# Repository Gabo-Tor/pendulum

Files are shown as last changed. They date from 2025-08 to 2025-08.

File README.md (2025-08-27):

# Actuated Pendulum with Propeller

A robot designed for reinforcement learning and control experiments with real hardware.

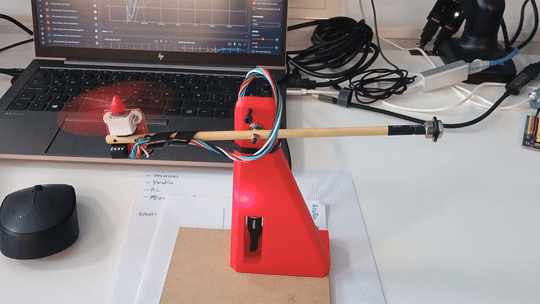
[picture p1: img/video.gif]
Video


# Repository Map

* **train.py**: training script for the robot.
* **hardware/**: 3D-printable models for the structure.
* **firmware/**: Arduino code for the ESP32 microcontroller.
* **test\_robot.py**: testing script for the robot.
* **env.py**: Gymnasium environment definition.
* **wrappers.py**: environment wrappers.

# Getting Started

## Hardware

### Bill of Materials

| Item | Description |
| --- | --- |
| ESP32 (Dev Kit C) | Microcontroller. Several board sizes are available on the market. We use the 25.70 × 53.40 mm version, but you may need to adapt the design for your board. |
| MG996R + propeller kit | Servo with motor, propeller, and controller. |
| AS5600 | Rotary encoder. |
| [3D-printed structure](hardware/body.stl) | Printed support structure. |
| 2 × M3 locking nuts | Fasteners. |
| 2 × M3×25 screws | Fasteners. |
| 623z | Bearing. |
| Flexible 4-wire cable | Electrical connection. |
| Wooden or cardboard base | Base, approximately 120 × 100 mm. |
| Counterweight | It has to still fall when left alone, but helps the actuator lift the pendulum. A M6 bolt, washer and nut was used in our case. |

### Assembly

* Connect the VCC pins of the MG996R and AS5600 to the 3.3 V pin on the ESP32.
* Connect all GND pins together, and w
* Connect the signal pins to the appropriate GPIOs on the ESP32 (as specified in *firmware.ino*).
* Glue the encoder magnet to the end of the screw that acts as the shaft.
* Some boards may require a small amount of glue to remain securely in place.

Assembled Robot

## Firmware

Upload the firmware to the ESP32 using the Arduino IDE.

## Usage

1. Install the required Python packages:

   ```bash
   pip install -r requirements.txt
   ```
2. Verify that everything is working by running:

   ```bash
   python test_robot.py
   ```

   The robot should move in a somewhat random manner.
3. Start training with:

   ```bash
   python train.py
   ```

# Reinforcement Learning

## History Wrapper

A history wrapper is used to maintain the last observations and actions taken by the agent.
This provides the agent with short-term memory and context, effectively restoring the Markov property of the environment. This is necessary because certain state variables (such as \$\dot{\theta}\$ or the propeller speed) are not directly observable from a single timestep.

## State-Space Representation

If we assume the propeller speed \$\omega\_p\$ is directly controllable (not entirely realistic), the system can be represented as:

$$
\mathbf{x} = \begin{bmatrix}\theta\\ \dot\theta\end{bmatrix},\qquad \omega_p = f(u).
$$

Dynamics:

$$
\dot{\mathbf{x}} =
\begin{bmatrix}
\dot\theta \\
\displaystyle \frac{1}{J}\Big( lc_T\omega_p^2 - m g l \sin\theta - b\dot\theta \Big)
\end{bmatrix}
$$

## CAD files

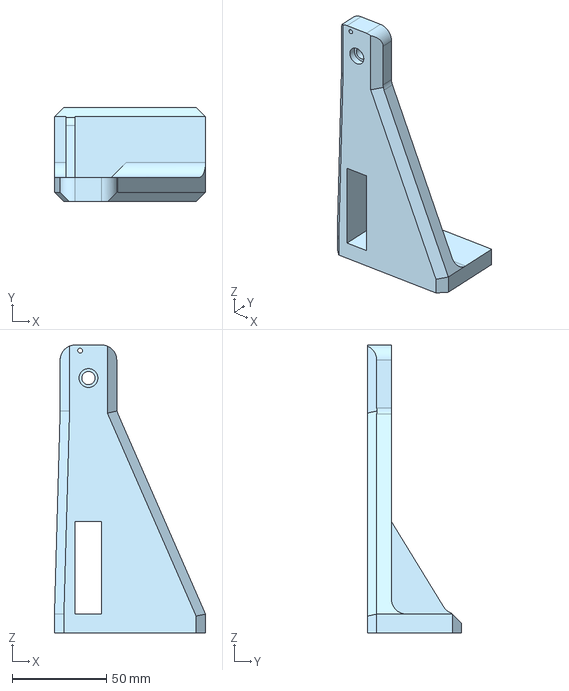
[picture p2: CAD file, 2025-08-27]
hardware/body.step
80.0 x 50.0 x 152.5 mm

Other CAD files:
hardware/body.stl

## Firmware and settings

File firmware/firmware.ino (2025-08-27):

#include <Wire.h>
#include "AS5600.h"

// === Pin Definitions ===
#define A_IN1 19   // L9110H Motor Driver INA
#define A_IN2 18   // L9110H Motor Driver INB
#define SDA 21  // I2C SDA pin for AS5600
#define SCL 22  // I2C SCL pin for AS5600

// === Constants ===
#define ZERO_ANGLE_OFFSET 869           // Calibration offset (raw units from AS5600) 0 is vertical
#define MAX_MOTOR_SPEED   255           // Max PWM value
#define MIN_MOTOR_SPEED   0

// === Globals ===
AS5600 as5600;
int currentMotorCmd = 0;  // Last received command (range -255 to 255)

// === Helper Functions ===

// Set motor output based on command value
void setMotor(int cmd) {
  cmd = constrain(cmd, -MAX_MOTOR_SPEED, MAX_MOTOR_SPEED);

  if (cmd > 0) {
    analogWrite(A_IN1, cmd);
    analogWrite(A_IN2, 0);
  } else if (cmd < 0) {
    analogWrite(A_IN1, 0);
    analogWrite(A_IN2, -cmd);  // use magnitude
  } else {
    analogWrite(A_IN1, 0);
    analogWrite(A_IN2, 0);
  }
}

// Read pendulum angle in degrees
float readAngle() {
  long rawAngle = as5600.readAngle();
  float angleDeg = (rawAngle - ZERO_ANGLE_OFFSET) * AS5600_RAW_TO_DEGREES;
  return angleDeg;
}

// Handle incoming serial command
void handleSerial() {
  if (Serial.available() > 0) {
    String input = Serial.readStringUntil('\n'); // Expect one line per action
    input.trim();

    if (input.length() > 0) {
      int cmd = input.toInt();   // Action = integer motor command
      currentMotorCmd = cmd;
      setMotor(currentMotorCmd);

      // Immediately respond with observation
      float angleDeg = readAngle();
      Serial.println(angleDeg, 3);  // report angle with 3 decimals
    }
  }
}

// === Arduino Setup ===
void setup() {
  // Motor pins
  pinMode(A_IN1, OUTPUT);
  pinMode(A_IN2, OUTPUT);

  // Serial + I2C
  Serial.begin(19200);
  Wire.begin(SDA, SCL);

  // Sensor setup
  as5600.begin(4);
  as5600.setDirection(AS5600_CLOCK_WISE);
  
  // Stop motor initially
  setMotor(0);
}

// === Arduino Loop ===
void loop() {
  handleSerial();  // Only act when command received
}

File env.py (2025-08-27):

import time

import gymnasium as gym
import numpy as np
import serial
from gymnasium import spaces


class RealPendulumEnv(gym.Env):
    """
    Gymnasium environment for a real pendulum controlled by ESP32 + AS5600.
    Fixed at 10 Hz control loop.
    Communication protocol:
      - Send: motor command as integer string + '\n'  (range -255..255)
      - Receive: angle in degrees as float string
    """
    metadata = {"render.modes": []}

    def __init__(self, port="/dev/ttyUSB0", baudrate=19200, max_episode_steps=200):
        super().__init__()

        # --- Serial connection ---
        self.ser = serial.Serial(port, baudrate, timeout=1)
        time.sleep(2.0)  # give ESP32 time to reset

        # --- Spaces ---
        self.action_space = spaces.Box(low=0.0, high=1.0, shape=(1,), dtype=np.float32)
        self.observation_space = spaces.Box(
            low=np.array([0.0], dtype=np.float32),
            high=np.array([np.pi], dtype=np.float32),
            dtype=np.float32,
        )

        # --- State ---
        self.max_episode_steps = max_episode_steps
        self.step_count = 0
        self.last_obs_deg = np.array([0.0], dtype=np.float32)
        self.last_action = 0.0
        self.last_step_time = None
        self.period = 0.1  # 10 Hz

    def _send_action(self, action: float):
        """Send action to ESP32 and get angle back."""
        pwm = int(np.clip(action, -1, 1) * 255)
        cmd = f"{pwm}\n".encode("utf-8")
        self.ser.write(cmd)

        line = self.ser.readline().decode("utf-8").strip()
        try:
            angle_deg = float(line)
        except ValueError:
            angle_deg = float(self.last_obs_deg[0])  # fallback to last obs

        angle_deg = np.clip(angle_deg, 0.0, 180.0)
        return np.array([angle_deg], dtype=np.float32)

    def step(self, action):
        self.step_count += 1

        # --- Send command immediately ---
        self.last_obs_deg = self._send_action(action[0])

        # --- Enforce 10 Hz timing ---
        now = time.time()
        if self.last_step_time is None:
            self.last_step_time = now

        elapsed = now - self.last_step_time
        remaining = self.period - elapsed

        if remaining > 0:
            time.sleep(remaining)
        else:
            print(f"[WARN] Step overran by {-remaining:.3f}s")

        self.last_step_time = time.time()

        angle_deg = float(self.last_obs_deg[0])
        angle_rad = np.deg2rad(angle_deg)

        # --- Reward ---
        angle_rew = np.sin(angle_rad) ** 2
        action_cost = (action[0] - 0.5) ** 2
        continuity_cost = (self.last_action - action[0]) ** 2

        reward = angle_rew - 0.5 * action_cost - 0.0 * continuity_cost

        terminated = False
        truncated = self.step_count >= self.max_episode_steps

        if truncated:
            self._send_action(0.0)

        self.last_action = action[0]

        return np.deg2rad(self.last_obs_deg), float(reward), terminated, truncated, {}

    def reset(self, seed=None, options=None):
        super().reset(seed=seed)
        self.step_count = 0

        # Reset motor
        self._send_action(0.0)
        time.sleep(1.0)

        # First obs
        self.last_obs_deg = self._send_action(0.0)
        self.last_step_time = time.time()
        return np.deg2rad(self.last_obs_deg), {}

    def close(self):
        if self.ser.is_open:
            self._send_action(0.0)
            self.ser.close()
